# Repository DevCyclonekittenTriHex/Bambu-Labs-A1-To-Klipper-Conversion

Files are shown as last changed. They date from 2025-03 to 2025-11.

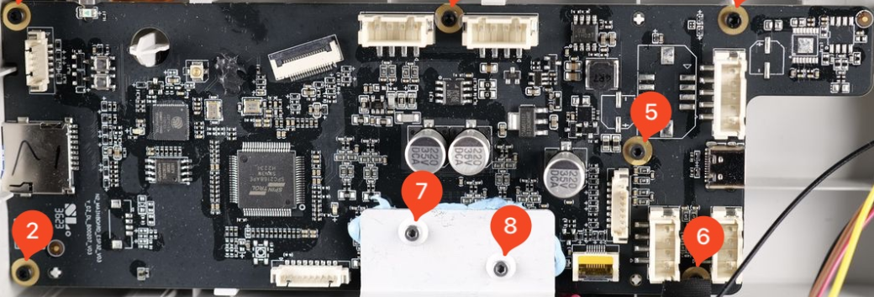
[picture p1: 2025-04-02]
OLDSTUFF/KicadImages/a1mb.png

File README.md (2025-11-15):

## Bambu Lab A1 Klipper Conversion (In development)

## Join Chaz's [**Discord Server**](https://discord.gg/W6B5mBejuC) to help with all bambu labs klipper mods.

> [!Caution]
> Doing any modifications may void your warrenty! 
> [!Caution]
> This Project is in currently not finished, this conversion is done fully at your own risk, I am not liable for any damages done to your machine.

This is constantly being updated, the docs for the conversion will be [Here!](https://devcyclonekittentrihex.github.io/A1K-Documentation/Docs/)

# Aim
The aim of this open source project is to create drop in circuit boards for the Bambu Labs A1 and A1 mini machines; and to provide a good framework to promote modding of these machines. This project will try to intergrate every part from the original printer to make the upgrade seamless. This will give back people privacy and a fully lan or offline system to print.

Currently, I have designed the a1 mainboard and a1/a1m toolhead boards, and am currently going through revisioning.
My target for the pcbs are to order them by November 30th

# Functions

Does work:
- Full hotend heating 
- XYZ Movement
- Stock Part Cooling Fans
- Auto Bed Levelling (with biqu microprobe)
- Filament Runout (with biqu sfs2)

Does not work:
- Heated Bed : Currently have the pinout for it, will be implemented in pcbs.
- Filament Sensor : It is a linear hall sensor, pinout unknown. Will attempt to find.
- AMS Lite : Closed source, other open mmus are compatible
- Display : An unidentified display that is possibly using 4SPI

# Previous Experiments
I previously hooked up an skr pico to the printer, and got it printing without a heated bed. Here is the footage. I also killed my mainboard so there is no more footage.
https://youtu.be/fLf-GMceLxE

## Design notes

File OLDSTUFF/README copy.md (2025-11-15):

## Bambu Lab A1 Klipper Conversion (In development)

## Join Chaz's [**Discord Server**](https://discord.gg/W6B5mBejuC) to help.

> [!Caution]
> Doing any modifications may void your warrenty!
> This Project is in currently not finished, this conversion is done fully at your own risk, I am not liable for any damages done to your machine. 

The aim of this project is to add klipper functional to the powerful Bambu Labs A1.
Due to the recent push for "privacy and security", people are wanting to add freedom back to their machines.

This is constantly being updated, the docs for the conversion will be [Here!](https://devcyclonekittentrihex.github.io/A1K-Documentation/Docs/)

# Functions that don't work:
If you have any imformation about this, please contact me.
- Filament Sensor : Its a ribbon cable with a linear hall sensor (detects magnets and is analoge)
- Display : (Unidentified Ribbon cable, bbl says on a1m page that its 4spi)
- AMS lite : Closed Source (possibly openamsl, or get open source mmu) 
- Heated Bed : I am unable to get a solid state relay currently, but it is really easy to do.
- Solid state relay board, it is controlled by a ribbon cable by 8, idk pinout.
- 
# PCBing:
I am currently working on some pcbs, the mainboard and toolhead board are nearly done but are encoutering some issues in development.
I will purchase through jlcpcb, the toolhead board price for 2 boards is around 60 aud without shipping.

# Current Progress
This is my 2nd print (voron cube first), the part cooling fan wasn't working in it and there was a layer shift.
https://youtu.be/fLf-GMceLxE

# EDIT, SKR PICO KILLED (20/07/2025)
I am stupid and somehow killed my skr pico, this is probs gonna add a 2 week delay.

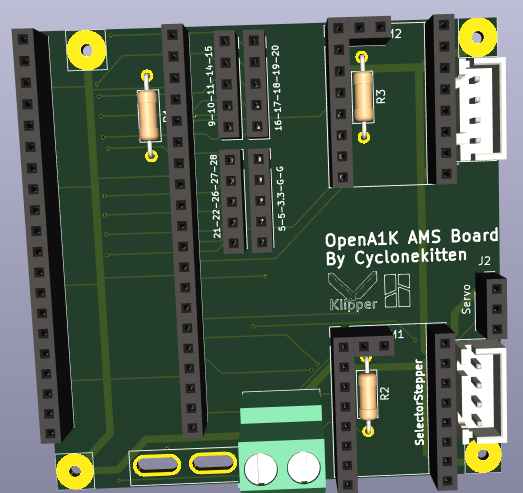
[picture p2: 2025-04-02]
OLDSTUFF/KicadImages/OpenA1K_AMSBoard.png

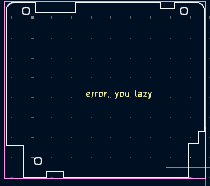
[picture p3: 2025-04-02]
OLDSTUFF/KicadImages/OpenA1K_THBoard.png

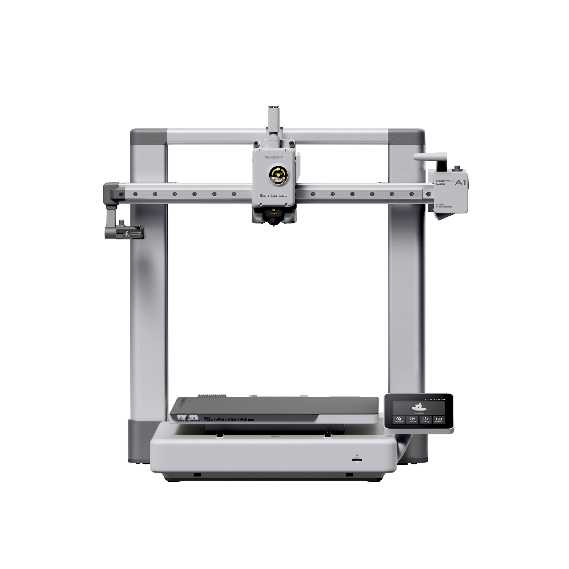
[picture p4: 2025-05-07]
OLDSTUFF/KicadImages/bbl_a1.png

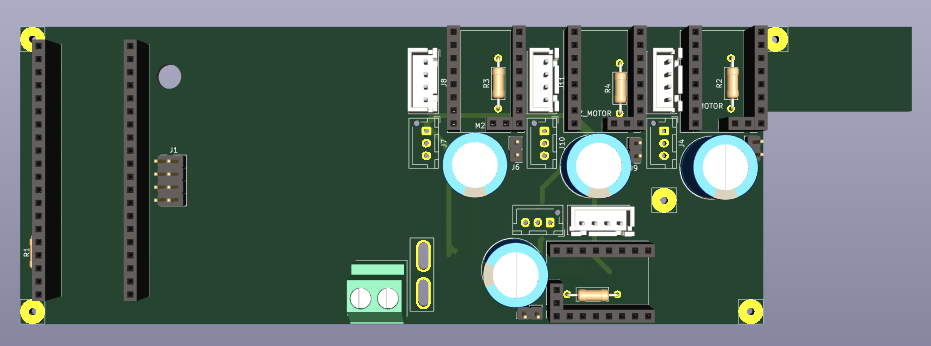
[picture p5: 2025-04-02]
OLDSTUFF/KicadImages/OpenA1K_MCUBoard.png

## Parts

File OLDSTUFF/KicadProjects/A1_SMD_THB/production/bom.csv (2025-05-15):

Designator | Footprint | Quantity | Value | LCSC Part #
C1, C4 | 0603 | 2 | 1uF | C15849
C10, C11, C14, C22, C28, C29, C3, C30, C5, C6, C7, C8, C9 | 0402 | 13 | 100nF
C12 | 0805 | 1 | 10uF | C15850
C13, C17, C18 | 0805 | 3 | 10uF
C15, C16 | 0402 | 2 | 15pF | C1548
C2 | 0402 | 1 | 100nF | C1525
C20, C25 | CP_Elec_8x10 | 2 | 100uF | C970687
C21 | 0603 | 1 | 22nF 50V | C21122
C23 | 0603 | 1 | 4.7uF | C19666
C24, C26 | 0603 | 2 | 100nF 50V
C27 | 0603 | 1 | 100nF 50V | C14663
D5 | SOT-23 | 1 | BAV99 | C2500
EXM2 | JST_XH_B4B-XH-A_1x04_P2.50mm_Vertical | 1 | Conn_01x04
J1 | PinHeader_1x02_P2.54mm_Vertical | 1 | Conn_01x02_Pin
J16 | PinHeader_1x01_P2.54mm_Vertical | 1 | SFS1
J2 | PinHeader_1x04_P2.54mm_Vertical | 1 | Conn_01x04_Pin
J3 | JST_XH_B4B-XH-A_1x04_P2.50mm_Vertical | 1 | PCF
J4 | PinHeader_1x03_P2.54mm_Vertical | 1 | Conn_01x03_Pin
J5 | JST_XH_B5B-XH-A_1x05_P2.50mm_Vertical | 1 | EXF
J6 | JST_XH_B2B-XH-A_1x02_P2.50mm_Vertical | 1 | THO
J7 | JST_XH_B2B-XH-A_1x02_P2.50mm_Vertical | 1 | HE
J8 | JST_XH_B2B-XH-A_1x02_P2.50mm_Vertical | 1 | BL_PROBE
J9 | JST_XH_B3B-XH-A_1x03_P2.50mm_Vertical | 1 | BL_SERVO
P1 | USB_C_Receptacle_HCTL_HC-TYPE-C-16P-01A | 1 | USB_C_Plug | C165948
R1, R2 | 0402 | 2 | 27.4o | C26971
R10, R11, R12 | 0402 | 3 | 20kΩ | C25765
R3 | 0603 | 1 | 1ko | C21190
R5, R6 | 0603 | 2 | 1k | C21190
R8, R9 | 1206 | 2 | 100mΩ | C25334
U1 | QFN-56-1EP_7x7mm_P0.4mm_EP3.2x3.2mm | 1 | RP2040 | C2040
U2 | SOT-223-3_TabPin2 | 1 | NCP1117-1.5_SOT223
U3 | QFN50P500X500X90-29N | 1 | TMC2209-LA | C2150710
U4 | SOIC-8_5.3x5.3mm_P1.27mm | 1 | W25Q128JVS | C97521
Y1 | Crystal_SMD_Abracon_ABM8AIG-4Pin_3.2x2.5mm | 1 | ABM8-272-T3 | C20625731

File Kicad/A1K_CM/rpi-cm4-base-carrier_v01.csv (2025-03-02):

Reference | Quantity | Value | Footprint | Datasheet | Digi-Key_PN | MPN | Manufacturer | Part Description | AVAILABILITY | DESCRIPTION | MF | MP | PACKAGE | PRICE | STANDARD | Digi-Key_PN (Alt) | Field4 | Field5
CR1 | 1 | SMBJ5.0A-TR | footprints:SMBJ5.0A-TR |  | 497-3144-1-ND | SMBJ5.0A-TR | STMicroelectronics
D1 | 1 | LED Green | LED_SMD:LED_0603_1608Metric | ~ | 160-1478-1-ND | LTST-S270KGKT | Lite-On Inc. | Green 572nm LED Indication - Discrete 2.2V 2-SMD, No Lead
D2 | 1 | LED Red | LED_SMD:LED_0603_1608Metric | ~ | 160-1479-1-ND | LTST-S270KRKT | Lite-On Inc. | Red 620nm LED Indication - Discrete 2.2V 2-SMD, No Lead
J1 | 1 | DNP | Connector_PinHeader_2.54mm:PinHeader_1x10_P2.54mm_Vertical | ~
J2 | 1 | USB4105-GF-A | USB4105-GF-A:GCT_USB4105-GF-A |  | 2073-USB4105-GF-ACT-ND | USB4105-GF-A | GCT |  | Unavailable | USB - C _Type - C_ USB 2.0 Receptacle Connector 24 Position Surface Mount, Right Angle; Through Hole | Global Connector Technology | USB4105 | Package Analog Devices | None
J3 | 1 | SM04B-SRSS-TB(LF)(SN) | SM04B-SRSS-TB_LF__SN_:JST_SM04B-SRSS-TB(LF)(SN) |  | 455-1804-1-ND | SM04B-SRSS-TB(LF)(SN) | JST Sales America Inc. |  |  |  |  |  |  |  | Manufacturer recommendations
J4 | 1 | USB_OTG | CM4IO:USB_Micro-B_EDAC_UCON00686 | ~ | 609-4050-1-ND | 10103594-0001LF | Amphenol ICC (FCI)
JP1 | 1 | SolderJumper_2_Open | Jumper:SolderJumper-2_P1.3mm_Open_RoundedPad1.0x1.5mm | ~
Module1 | 1 | ComputeModule4-CM4 | CM4IO:Raspberry-Pi-4-Compute-Module |  | 2x H11615CT-ND | 2x DF40C-100DS-0.4V | Hirose |  |  |  |  |  |  |  |  | 2x H124602CT-ND | Hirose | 2x DF40C-100DS-0.4V
R1 R4 | 2 | 5.1k | Resistor_SMD:R_0603_1608Metric_Pad0.98x0.95mm_HandSolder | ~ | 311-5.10KHRCT-ND | RC0603FR-075K1L | Yageo
R2 R6 | 2 | 1k | Resistor_SMD:R_0603_1608Metric_Pad0.98x0.95mm_HandSolder | ~ | 311-1.00KHRCT-ND | RC0603FR-071KL | Yageo
R3 R5 | 2 | DNP | Resistor_SMD:R_0603_1608Metric_Pad0.98x0.95mm_HandSolder | ~
R7 R8 | 2 | 2.2K 1% | Resistor_SMD:R_0603_1608Metric_Pad0.98x0.95mm_HandSolder | ~ | 311-2.20KHRCT-ND | RC0603FR-072K2L | Yageo
U1 | 1 | 74LVC1G07SE-7 | Package_TO_SOT_SMD:SOT-353_SC-70-5 | http://www.ti.com/lit/sg/scyt129e/scyt129e.pdf | 74LVC1G07SE-7DICT-ND | 74LVC1G07SE-7 | Diodes Incorporated | Buffer, Non-Inverting 1 Element 1 Bit per Element Open Drain Output SOT-353
U2 | 1 | TPD2EUSB30 | Package_TO_SOT_SMD:Texas_DRT-3 | http://www.ti.com/lit/ds/symlink/tpd2eusb30a.pdf | 296-25509-1-ND | TPD2EUSB30DRTR | Texas Instruments

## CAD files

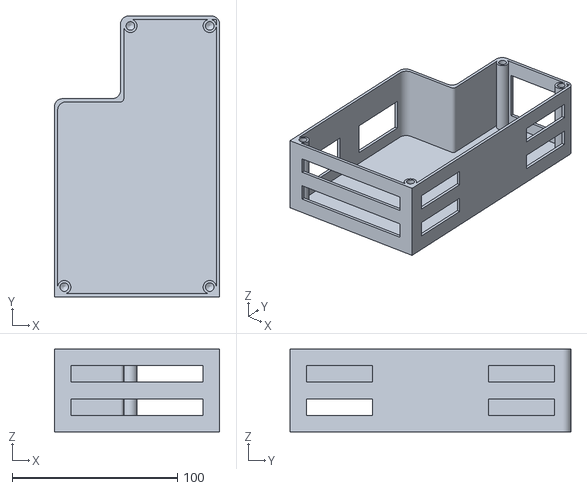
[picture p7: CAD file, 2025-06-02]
OLDSTUFF/PrintedFiles/Upgrades/mainboard_box-Body001.stl
100.0 x 170.0 x 50.0

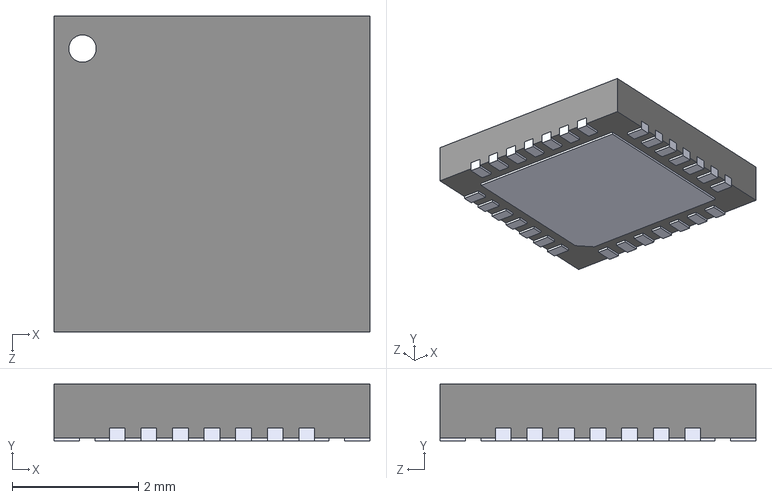
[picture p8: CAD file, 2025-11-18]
A1-Main-Board/footprints/TMC2209-LA.step
5.00 x 0.9 x 5.00 mm

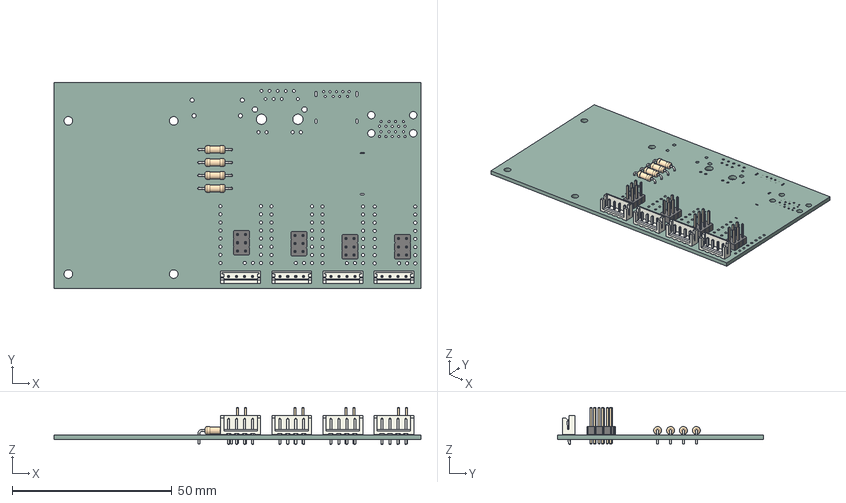
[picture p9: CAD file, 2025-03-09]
Kicad/A1K_CM/rpi-cm4-base-carrier.step
115.0 x 64.5 x 11.7 mm
JST_EH_B4B-EH-A_1x04_P2.50mm_Vertical x 4
PinHeader_2x03_P2.54mm_Vertical x 4
R_Axial_DIN0207_L6.3mm_D2.5mm_P10.16mm_Horizontal x 4
rpi-cm4-base-carrier_PCB

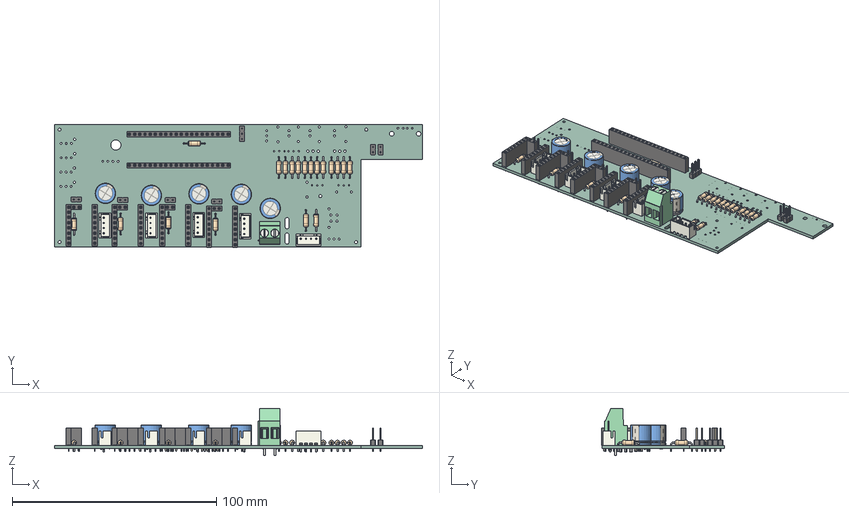
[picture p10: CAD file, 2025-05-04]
OLDSTUFF/KicadProjects/A1_MB.step
180.0 x 60.1 x 23.0 mm
JST_XH_B4B-XH-A_1x04_P2.50mm_Vertical x 5
R_Axial_DIN0207_L6.3mm_D2.5mm_P10.16mm_Horizontal x 19
PinHeader_1x02_P2.54mm_Vertical x 6
PinSocket_1x08_P2.54mm_Vertical x 8
PinSocket_1x02_P2.54mm_Vertical x 4
CP_Radial_D10.0mm_P5.00mm_P7.50mm x 5
PinHeader_1x03_P2.54mm_Vertical
PinSocket_1x20_P2.54mm_Vertical x 2
TerminalBlock_Phoenix_MKDS-3-2-5.08_1x02_P5.08mm_Horizontal
A1_MB_PCB

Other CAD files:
OLDSTUFF/PrintedFiles/Upgrades/mainboard_box.FCStd

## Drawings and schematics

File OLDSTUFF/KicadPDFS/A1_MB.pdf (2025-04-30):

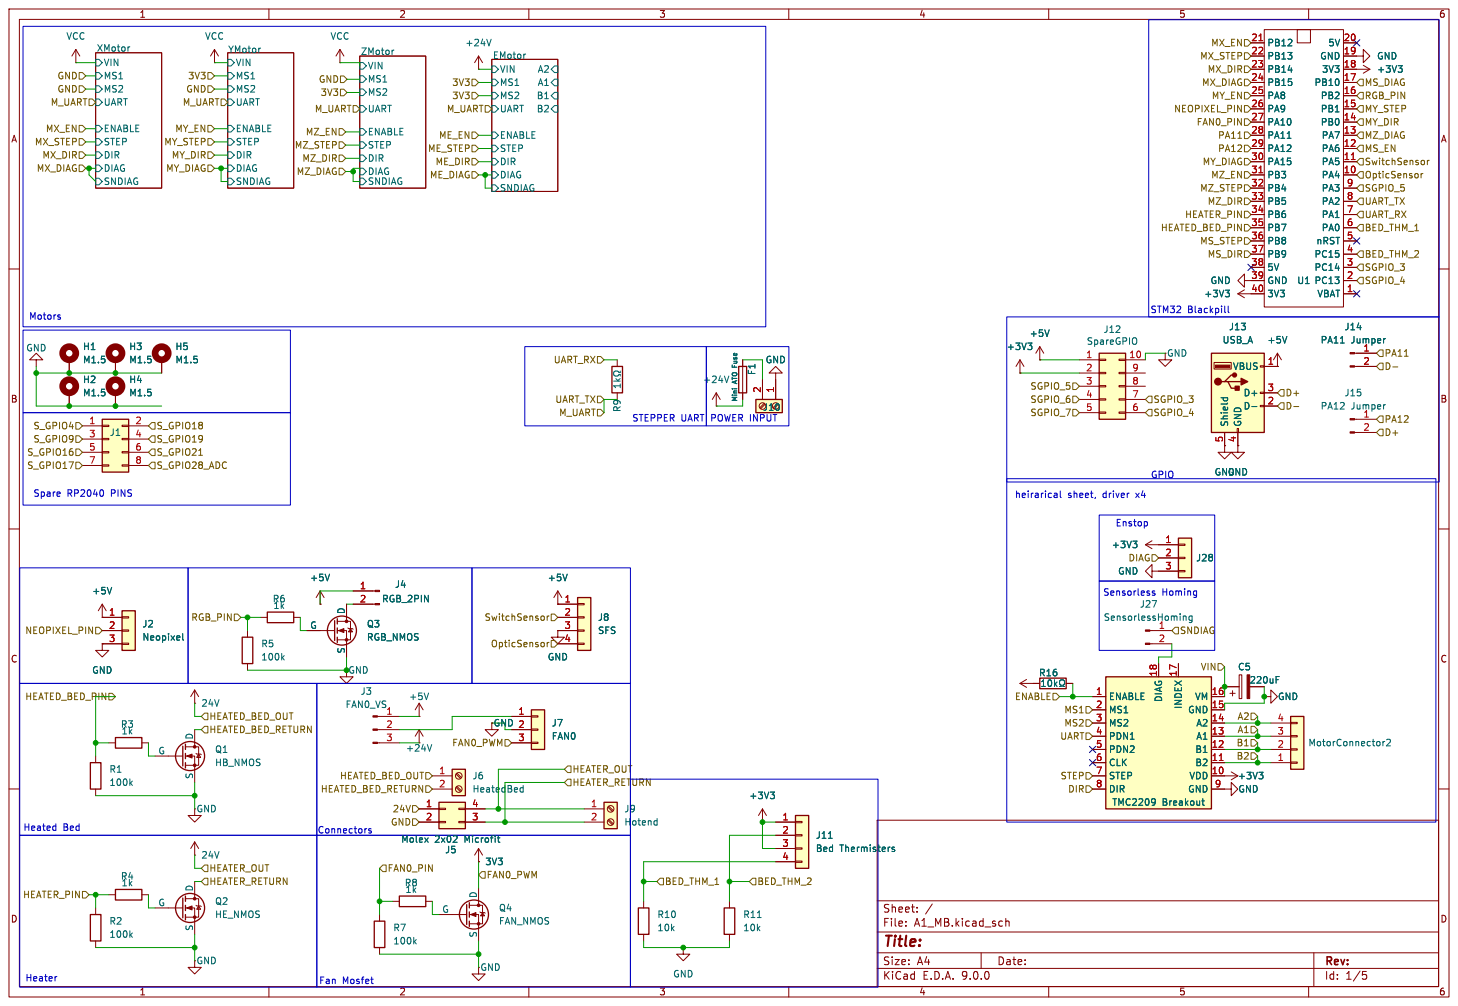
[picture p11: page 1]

Id: 1/5 Title: File: A1_MB.kicad_sch Sheet: /

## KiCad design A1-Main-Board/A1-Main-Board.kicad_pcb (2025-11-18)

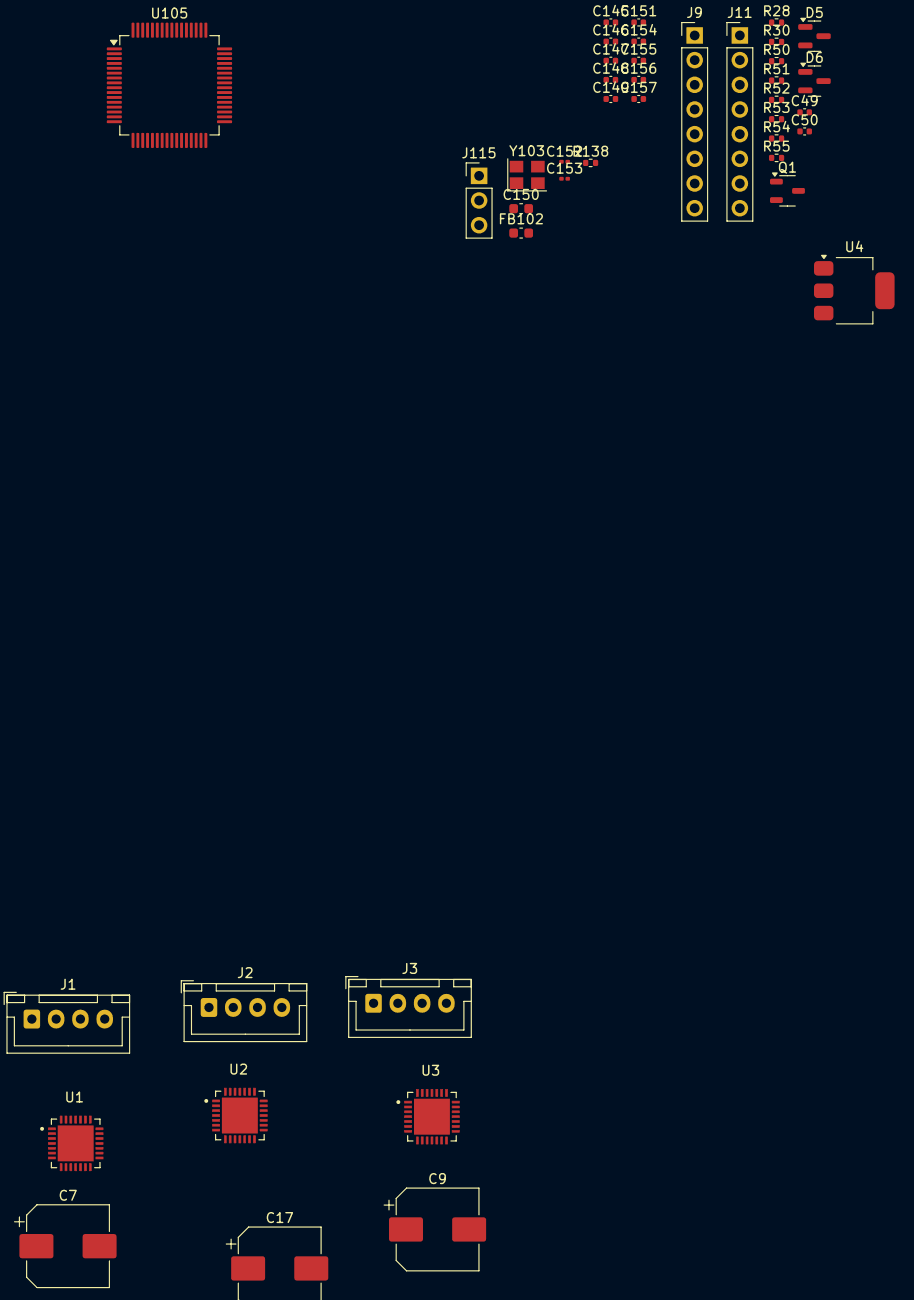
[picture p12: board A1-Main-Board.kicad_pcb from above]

Board: 2 copper layers, 43 parts (0 on the bottom side), 33 nets, no tracks yet.

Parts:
C7, C9, C17: 100uF; CP_Elec_8x10
C49, C50, C147, C148, C149, C154, C155, C156, C157: 100nF; C_0402_1005Metric
C145, C146: 30pF; C_0402_1005Metric
C150: 10uF; C_0603_1608Metric
C151: 10nF; C_0402_1005Metric
C152, C153: 1uF; C_0201_0603Metric
D5, D6: BAV99; SOT-23
FB102: 120r 100MHz; C_0603_1608Metric
J1, J2, J3: MotorJST; JST_XH_B4B-XH-A_1x04_P2.50mm_Vertical
J9: FPC1; PinHeader_1x08_P2.54mm_Vertical
J11: FPC2; PinHeader_1x08_P2.54mm_Vertical
J115: BOOT; PinHeader_1x03_P2.54mm_Vertical
Q1: NMOS; SOT-23-3
R28: 10R; R_0402_1005Metric
R30: 20kR; R_0402_1005Metric
R50, R53: 4.7kR; R_0402_1005Metric
R51, R52, R54, R55: 2.37kR; R_0402_1005Metric
R138: 10kR; R_0402_1005Metric
U1, U2, U3: TMC2209-LA
U4: AMS1117-3.3; SOT-223-3_TabPin2
U105: STM32G431RBT3; LQFP-64_10x10mm_P0.5mm
Y103: Crystal_GND24; Crystal_SMD_3225-4Pin_3.2x2.5mm

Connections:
+3V3: C147.1, C149.1, C150.1, C153.1, C154.1, C155.1, C156.1, C157.1, FB102.2, J115.1, U1.15 (VCC_IO), U2.9 (MS1_AD0), U2.15 (VCC_IO), U3.10 (MS2_AD1), U3.15 (VCC_IO), U105.1 (VBAT), U105.16 (VDD), U105.32 (VDD), U105.48 (VDD), U105.64 (VDD)
+3V3A: C151.1, C152.1, D5.2 (A), D6.2 (A), FB102.1, R50.1, R53.1, U105.28 (VREF+), U105.29 (VDDA)
+5V: J11.1, U1.8 (5VOUT), U2.8 (5VOUT), U3.8 (5VOUT)
+24V: C7.1, C9.1, C17.1, U1.22 (VS), U1.28 (VS), U2.22 (VS), U2.28 (VS), U3.22 (VS), U3.28 (VS)
/drivers/MA_UART: U1.14 (~PD_UART), U2.14 (~PD_UART), U3.14 (~PD_UART), U105.22 (PC4)
/heated-bed/10k_THB_INP: J11.4, R53.2, R54.1
/heated-bed/100k_THB_INP: J11.2, R50.2, R51.1
/heated-bed/BED_THERM_1: C49.1, R52.2, U105.36 (PB14)
/heated-bed/BED_THERM_2: C50.1, R55.2, U105.43 (PA9)
/heated-bed/HEATED_BED-: J11.7, Q1.1 (D)
/heated-bed/HEATED_BED_PWM: R28.1, R30.1, U105.38 (PC6)
GND: C7.2, C9.2, C17.2, C49.2, C50.2, C145.2, C146.2, C148.2, C151.2, C152.2, C153.2, D5.1 (K), D6.1 (K), J11.3, J11.5, J11.8, J115.3, Q1.3 (S), R30.2, U1.3 (GND), U1.9 (MS1_AD0), U1.10 (MS2_AD1), U1.18 (GND), U1.29 (EXP), U2.3 (GND), U2.10 (MS2_AD1), U2.18 (GND), U2.29 (EXP), U3.3 (GND), U3.9 (MS1_AD0), U3.18 (GND), U3.29 (EXP), U105.15 (VSS), U105.27 (VSSA), U105.31 (VSS), U105.47 (VSS), U105.63 (VSS), Y103.2, Y103.4
unnamed: C147.2, C149.2, C150.2, C154.2, C155.2, C156.2, C157.2
unnamed: D5.3 (K), R51.2, R52.1
unnamed: D6.3 (K), R54.2, R55.1
unnamed: J1.1, U1.24 (OA1)
unnamed: J1.2, U1.26 (OB1)
unnamed: J1.3, U1.21 (OA2)
unnamed: J1.4, U1.1 (OB2)
unnamed: J2.1, U2.24 (OA1)
unnamed: J2.2, U2.26 (OB1)
unnamed: J2.3, U2.21 (OA2)
unnamed: J2.4, U2.1 (OB2)
unnamed: J3.1, U3.24 (OA1)
unnamed: J3.2, U3.26 (OB1)
unnamed: J3.3, U3.21 (OA2)
unnamed: J3.4, U3.1 (OB2)
unnamed: J115.2, R138.1
unnamed: Q1.2 (G), R28.2
unnamed: C148.1, U105.7 (PG10)
unnamed: R138.2, U105.61 (PB8)
unnamed: C145.1, U105.5 (PF0), Y103.1
unnamed: C146.1, U105.6 (PF1), Y103.3

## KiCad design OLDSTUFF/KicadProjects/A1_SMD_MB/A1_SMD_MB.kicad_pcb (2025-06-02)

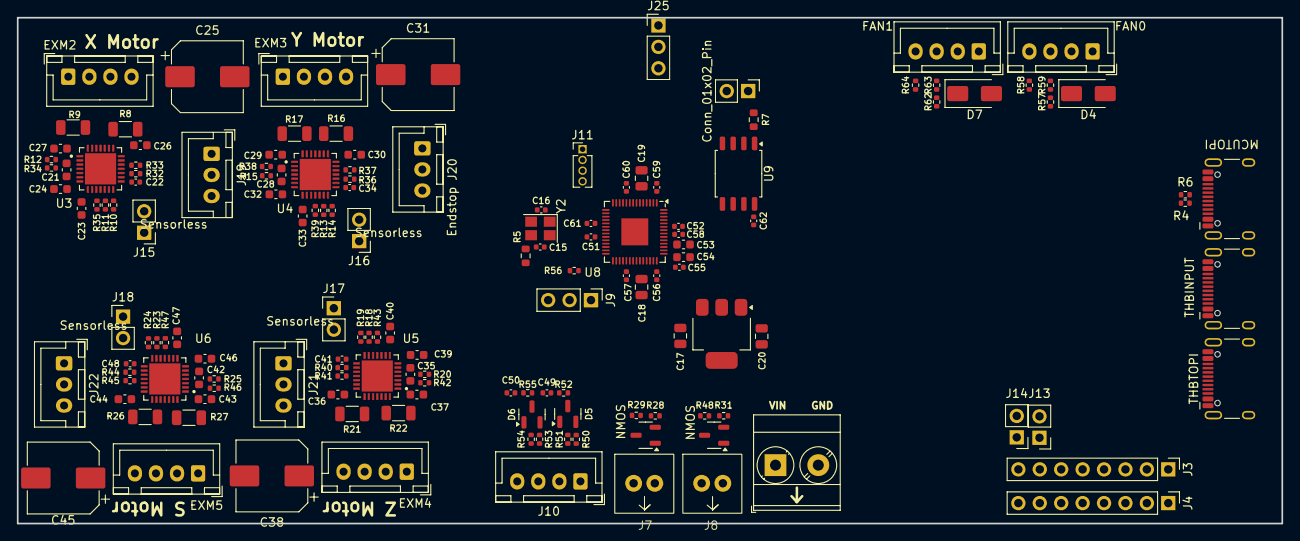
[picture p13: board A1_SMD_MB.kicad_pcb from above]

Board: 2 copper layers, 150.0 x 60.0 mm, 148 parts (0 on the bottom side), 134 nets, no tracks yet.

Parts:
C15, C16: 15pF; C_0402_1005Metric
C17, C18, C19, C20: 10uF; C_0805_2012Metric
C21, C28, C35, C42: 22nF 50V; C_0603_1608Metric
C22, C34, C41, C48, C49, C50, C51, C52, C55, C56, C57, C58, C59, C60, C61, C62: 100nF; C_0402_1005Metric
C23, C33, C40, C47: 4.7uF; C_0603_1608Metric
C24, C26, C27, C29, C30, C32, C36, C37, C39, C43, C44, C46: 100nF 50V; C_0603_1608Metric
C25, C31, C38, C45: 100uF; CP_Elec_8x10
C53, C54: 1uF; C_0603_1608Metric
D4, D7: D; D_SMA
D5, D6: BAV99; SOT-23
EXM2, EXM3, EXM4, EXM5: Conn_01x04; JST_XH_B4B-XH-A_1x04_P2.50mm_Vertical
J3: FPC2; PinHeader_1x08_P2.54mm_Vertical
J4: FPC1; PinHeader_1x08_P2.54mm_Vertical
J6: FAN0; JST_XH_B4B-XH-A_1x04_P2.50mm_Vertical
J7: HE; ScrewTerminal 7mm x 7mm
J8: HB; ScrewTerminal 7mm x 7mm
J9: Conn_01x03_Pin; PinHeader_1x03_P2.54mm_Vertical
J10: BedTherms; JST_XH_B4B-XH-A_1x04_P2.50mm_Vertical
J11: SWD; PinHeader_1x04_P1.27mm_Vertical
J12: Conn_01x02_Pin; PinHeader_1x02_P2.54mm_Vertical
J13: THM2JMP; PinHeader_1x02_P2.54mm_Vertical
J14: THM1JMP; PinHeader_1x02_P2.54mm_Vertical
J15, J16, J17, J18: Sensorless; PinHeader_1x02_P2.54mm_Vertical
J19, J20, J21, J22: Endstop; JST_XH_B3B-XH-A_1x03_P2.50mm_Vertical
J23: PWR; 1x2 Terminal Block
J24: FAN1; JST_XH_B4B-XH-A_1x04_P2.50mm_Vertical
J25: SPR_IO; PinHeader_1x03_P2.54mm_Vertical
P1: MCUTOPI; USB_C_Receptacle_HCTL_HC-TYPE-C-16P-01A
P2: THBINPUT; USB_C_Receptacle_HCTL_HC-TYPE-C-16P-01A
P3: THBTOPI; USB_C_Receptacle_HCTL_HC-TYPE-C-16P-01A
Q1, Q2: NMOS; SOT-23-3
R4, R6: 27.4o; R_0402_1005Metric
R5: 1k; R_0603_1608Metric
R7: 1ko; R_0603_1608Metric
R8, R9, R16, R17, R21, R22, R26, R27: 100mΩ; R_1206_3216Metric
R10, R11, R12, R13, R14, R15, R18, R19, R20, R23, R24, R25: 20kΩ; R_0402_1005Metric
R28, R31: 10R; R_0402_1005Metric
R29, R48, R58, R64: 20kR; R_0402_1005Metric
R32, R33, R34, R35, R36, R37, R38, R39, R40, R41, R42, R43, R44, R45, R46, R47: 100o; R_0402_1005Metric
R50, R53: 4.7kR; R_0402_1005Metric
R51, R52, R54, R55: 2.37kR; R_0402_1005Metric
R56: 10k; R_0402_1005Metric
R57, R59, R62, R63: 100R; R_0402_1005Metric
U3, U4, U5, U6: TMC2209-LA
U7: NCP1117-1.5_SOT223; SOT-223-3_TabPin2
U8: RP2040; QFN-56-1EP_7x7mm_P0.4mm_EP3.2x3.2mm
U9: W25Q128JVS; SOIC-8_5.3x5.3mm_P1.27mm
Y2: ABM8-272-T3; Crystal_SMD_Abracon_ABM8AIG-4Pin_3.2x2.5mm

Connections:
+1V1: C51.1, C52.1, C53.1, U8.23 (DVDD), U8.45 (VREG_VOUT), U8.50 (DVDD)
+3.3VADC: D5.2 (A), D6.2 (A), R50.1, R53.1
+3V3: C18.1, C19.1, C20.1, C22.2, C34.2, C41.2, C48.2, C54.1, C55.1, C56.1, C57.1, C58.1, C59.1, C60.1, C61.1, C62.1, J3.5, J9.1, J11.1, R12.1, R15.1, R20.1, R25.1, U3.15 (VCC_IO), U4.9 (MS1_AD0), U4.15 (VCC_IO), U5.10 (MS2_AD1), U5.15 (VCC_IO), U6.9 (MS1_AD0), U6.10 (MS2_AD1), U6.15 (VCC_IO), U7.2 (VO), U8.1 (IOVDD), U8.10 (IOVDD), U8.22 (IOVDD), U8.33 (IOVDD), U8.42 (IOVDD), U8.43 (ADC_AVDD), U8.44 (VREG_IN), U8.48 (USB_VDD), U8.49 (IOVDD), U9.8 (VCC)
+5V: C23.2, C33.2, C40.2, C47.2, J3.1, J3.2, J19.3, J20.3, J21.3, J22.3, P2.A8 (SBU1), P2.B8 (SBU2), U3.8 (5VOUT), U4.8 (5VOUT), U5.8 (5VOUT), U6.8 (5VOUT)
+24V: C24.1, C25.1, C26.2, C27.2, C29.2, C30.2, C31.1, C32.1, C36.2, C37.2, C38.1, C39.1, C43.2, C44.2, C45.1, C46.1, D4.2 (A), D7.2 (A), J6.1, J7.1, J8.1, J23.1, J24.1, P2.A4 (VBUS), P2.A9 (VBUS), P2.B4 (VBUS), P2.B9 (VBUS), U3.22 (VS), U3.28 (VS), U4.22 (VS), U4.28 (VS), U5.22 (VS), U5.28 (VS), U6.22 (VS), U6.28 (VS)
/Motors/MS_DIAG: J22.1, R47.2, U8.34 (GPIO22)
/Motors/MS_DIR: R45.1, U8.32 (GPIO21)
/Motors/MS_EN: R46.1, U8.30 (GPIO19)
/Motors/MS_STEP: R44.1, U8.31 (GPIO20)
/Motors/MX_DIAG: J19.1, R35.2, U8.13 (GPIO10)
/Motors/MX_DIR: R33.1, U8.12 (GPIO9)
/Motors/MX_EN: R34.1, U8.9 (GPIO7)
/Motors/MX_STEP: R32.1, U8.11 (GPIO8)
/Motors/MY_DIAG: J20.1, R39.2, U8.17 (GPIO14)
/Motors/MY_DIR: R37.1, U8.16 (GPIO13)
/Motors/MY_EN: R38.1, U8.14 (GPIO11)
/Motors/MY_STEP: R36.1, U8.15 (GPIO12)
/Motors/MZ_DIAG: J21.1, R43.2, U8.29 (GPIO18)
/Motors/MZ_DIR: R41.1, U8.28 (GPIO17)
/Motors/MZ_EN: R42.1, U8.18 (GPIO15)
/Motors/MZ_STEP: R40.1, U8.27 (GPIO16)
/Motors/UART: R10.2, R14.2, R19.2, R24.2, U3.14 (~PD_UART), U4.14 (~PD_UART), U5.14 (~PD_UART), U6.14 (~PD_UART), U8.8 (GPIO6)
/fpc/HB_CT: J3.6, U8.6 (GPIO4)
/fpc/THM1: C50.1, J14.2, R55.2, U8.41 (GPIO29_ADC3)
/fpc/THM2: C49.1, J13.2, R52.2, U8.40 (GPIO28_ADC2)
/mcu/G1: R58.1, U8.3 (GPIO1)
/mcu/G2: R31.1, R48.1, U8.4 (GPIO2)
/mcu/G3: R28.1, R29.1, U8.5 (GPIO3)
/mcu/G23: J25.1, U8.35 (GPIO23)
/mcu/G24: J25.2, U8.36 (GPIO24)
/mcu/G25: J25.3, U8.37 (GPIO25)
/mcu/G26: R62.1, U8.38 (GPIO26_ADC0)
/mcu/G27: R64.1, U8.39 (GPIO27_ADC1)
/mcu/GPIO0: R57.1, U8.2 (GPIO0)
/mcu/IO0: U8.53 (QSPI_SD0), U9.5 (DI/IO_{0})
/mcu/IO1: U8.55 (QSPI_SD1), U9.2 (DO/IO_{1})
/mcu/IO2: U8.54 (QSPI_SD2), U9.3 (~WP/IO_{2})
/mcu/IO3: U8.51 (QSPI_SD3), U9.7 (~HOLD/~RESET/IO_{3})
/mcu/IO_CLK: U8.52 (QSPI_SCLK), U9.6 (CLK)
/mcu/IO_CS: R7.2, U8.56 (QSPI_SS), U9.1 (~CS)
/mcu/USB_D+: P1.A6 (D+), R4.1
/mcu/USB_D-: P1.A7 (D-), R6.1
/mcu/XIN: C16.2, U8.20 (XIN), Y2.1
/mcu/XOUT: R5.2, U8.21 (XOUT)
/stuff/HB_S: Q2.2 (G), R31.2
/stuff/HE_S: Q1.2 (G), R28.2
GND: C22.1, C23.1, C25.2, C26.1, C27.1, C29.1, C30.1, C31.2, C33.1, C34.1, C36.1, C37.1, C38.2, C40.1, C41.1, C43.1, C44.1, C45.2, C47.1, C48.1, C49.2, C50.2, D4.1 (K), D5.1 (K), D6.1 (K), D7.1 (K), J3.3, J3.4, J6.2, J10.2, J10.4, J19.2, J20.2, J21.2, J22.2, J23.2, J24.2, P1.A1 (GND), P1.A12 (GND), P1.B1 (GND), P1.B12 (GND), P1.S1 (SHIELD), P2.A1 (GND), P2.A12 (GND), P2.B1 (GND), P2.B12 (GND), P2.S1 (SHIELD), P3.A1 (GND), P3.A12 (GND), P3.B1 (GND), P3.B12 (GND), P3.S1 (SHIELD), Q1.3 (S), Q2.3 (S), R8.2, R9.2, R10.1, R11.1, R13.1, R14.1, R16.2, R17.2, R18.1, R19.1, R21.2, R22.2, R23.1, R24.1, R26.2, R27.2, R29.2, R48.2, U3.3 (GND), U3.9 (MS1_AD0), U3.10 (MS2_AD1), U3.18 (GND), U3.29 (EXP), U4.3 (GND), U4.10 (MS2_AD1), U4.18 (GND), U4.29 (EXP), U5.3 (GND), U5.9 (MS1_AD0), U5.18 (GND), U5.29 (EXP), U6.3 (GND), U6.18 (GND), U6.29 (EXP)
GND3: C15.1, C16.1, C17.2, C18.2, C19.2, C20.2, C51.2, C52.2, C53.2, C54.2, C55.2, C56.2, C57.2, C58.2, C59.2, C60.2, C61.2, C62.2, J9.3, J11.4, J12.2, U7.1 (GND), U8.19 (TESTEN), U8.57 (GND), U9.4 (GND), Y2.2, Y2.4
unnamed: C15.2, R5.1, Y2.3
unnamed: D5.3 (K), R51.2, R52.1
unnamed: D6.3 (K), R54.2, R55.1
unnamed: EXM2.1, U3.1 (OB2)
unnamed: EXM2.2, U3.26 (OB1)
unnamed: EXM2.3, U3.24 (OA1)
unnamed: EXM2.4, U3.21 (OA2)
unnamed: EXM3.1, U4.1 (OB2)
unnamed: EXM3.2, U4.26 (OB1)
unnamed: EXM3.3, U4.24 (OA1)
unnamed: EXM3.4, U4.21 (OA2)
unnamed: EXM4.1, U5.1 (OB2)
unnamed: EXM4.2, U5.26 (OB1)
unnamed: EXM4.3, U5.24 (OA1)
unnamed: EXM4.4, U5.21 (OA2)
unnamed: EXM5.1, U6.1 (OB2)
unnamed: EXM5.2, U6.26 (OB1)
unnamed: EXM5.3, U6.24 (OA1)
unnamed: EXM5.4, U6.21 (OA2)
unnamed: J6.3, R59.2
unnamed: J6.4, R58.2
unnamed: J7.2, Q1.1 (D)
unnamed: J8.2, Q2.1 (D)
unnamed: J9.2, R56.1
unnamed: J10.1, R50.2, R51.1
unnamed: J10.3, R53.2, R54.1
unnamed: J11.2, U8.24 (SWCLK)
unnamed: J11.3, U8.25 (SWD)
unnamed: J12.1, R7.1
unnamed: J3.7, J13.1
unnamed: J3.8, J14.1
unnamed: J15.1, R35.1
unnamed: J15.2, U3.11 (DIAG)
unnamed: J16.1, R39.1
unnamed: J16.2, U4.11 (DIAG)
unnamed: J17.1, R43.1
unnamed: J17.2, U5.11 (DIAG)
unnamed: J18.1, R47.1
unnamed: J18.2, U6.11 (DIAG)
unnamed: J24.3, R63.2
unnamed: J24.4, R64.2
unnamed: P2.A5 (CC), P2.B5 (VCONN)
unnamed: P2.A6 (D+), P3.A6 (D+)
unnamed: P2.A7 (D-), P3.A7 (D-)
unnamed: R57.2, R59.1
unnamed: R62.2, R63.1
unnamed: R8.1, U3.23 (BRA)
unnamed: R9.1, U3.27 (BRB)
unnamed: R11.2, U3.13 (CLK)
unnamed: C21.1, U3.5 (CPI)
unnamed: C21.2, U3.4 (CPO)
unnamed: R33.2, U3.19 (DIR)
unnamed: R32.2, U3.16 (STEP)
unnamed: C24.2, U3.6 (VCP)
unnamed: R12.2, R34.2, U3.2 (~EN)
unnamed: R16.1, U4.23 (BRA)
unnamed: R17.1, U4.27 (BRB)
unnamed: R13.2, U4.13 (CLK)
unnamed: C28.1, U4.5 (CPI)
unnamed: C28.2, U4.4 (CPO)
unnamed: R37.2, U4.19 (DIR)
unnamed: R36.2, U4.16 (STEP)
unnamed: C32.2, U4.6 (VCP)
unnamed: R15.2, R38.2, U4.2 (~EN)
unnamed: R21.1, U5.23 (BRA)
unnamed: R22.1, U5.27 (BRB)
unnamed: R18.2, U5.13 (CLK)
unnamed: C35.1, U5.5 (CPI)
unnamed: C35.2, U5.4 (CPO)
unnamed: R41.2, U5.19 (DIR)
unnamed: R40.2, U5.16 (STEP)
unnamed: C39.2, U5.6 (VCP)
unnamed: R20.2, R42.2, U5.2 (~EN)
unnamed: R26.1, U6.23 (BRA)
unnamed: R27.1, U6.27 (BRB)
unnamed: R23.2, U6.13 (CLK)
unnamed: C42.1, U6.5 (CPI)
unnamed: C42.2, U6.4 (CPO)
unnamed: R45.2, U6.19 (DIR)
unnamed: R44.2, U6.16 (STEP)
unnamed: C46.2, U6.6 (VCP)
unnamed: R25.2, R46.2, U6.2 (~EN)
unnamed: R56.2, U8.26 (RUN)
unnamed: R6.2, U8.46 (USB_DM)
unnamed: R4.2, U8.47 (USB_DP)
VBUS: C17.1, P1.A4 (VBUS), P1.A9 (VBUS), P1.B4 (VBUS), P1.B9 (VBUS), P3.A4 (VBUS), P3.A9 (VBUS), P3.B4 (VBUS), P3.B9 (VBUS), U7.3 (VI)

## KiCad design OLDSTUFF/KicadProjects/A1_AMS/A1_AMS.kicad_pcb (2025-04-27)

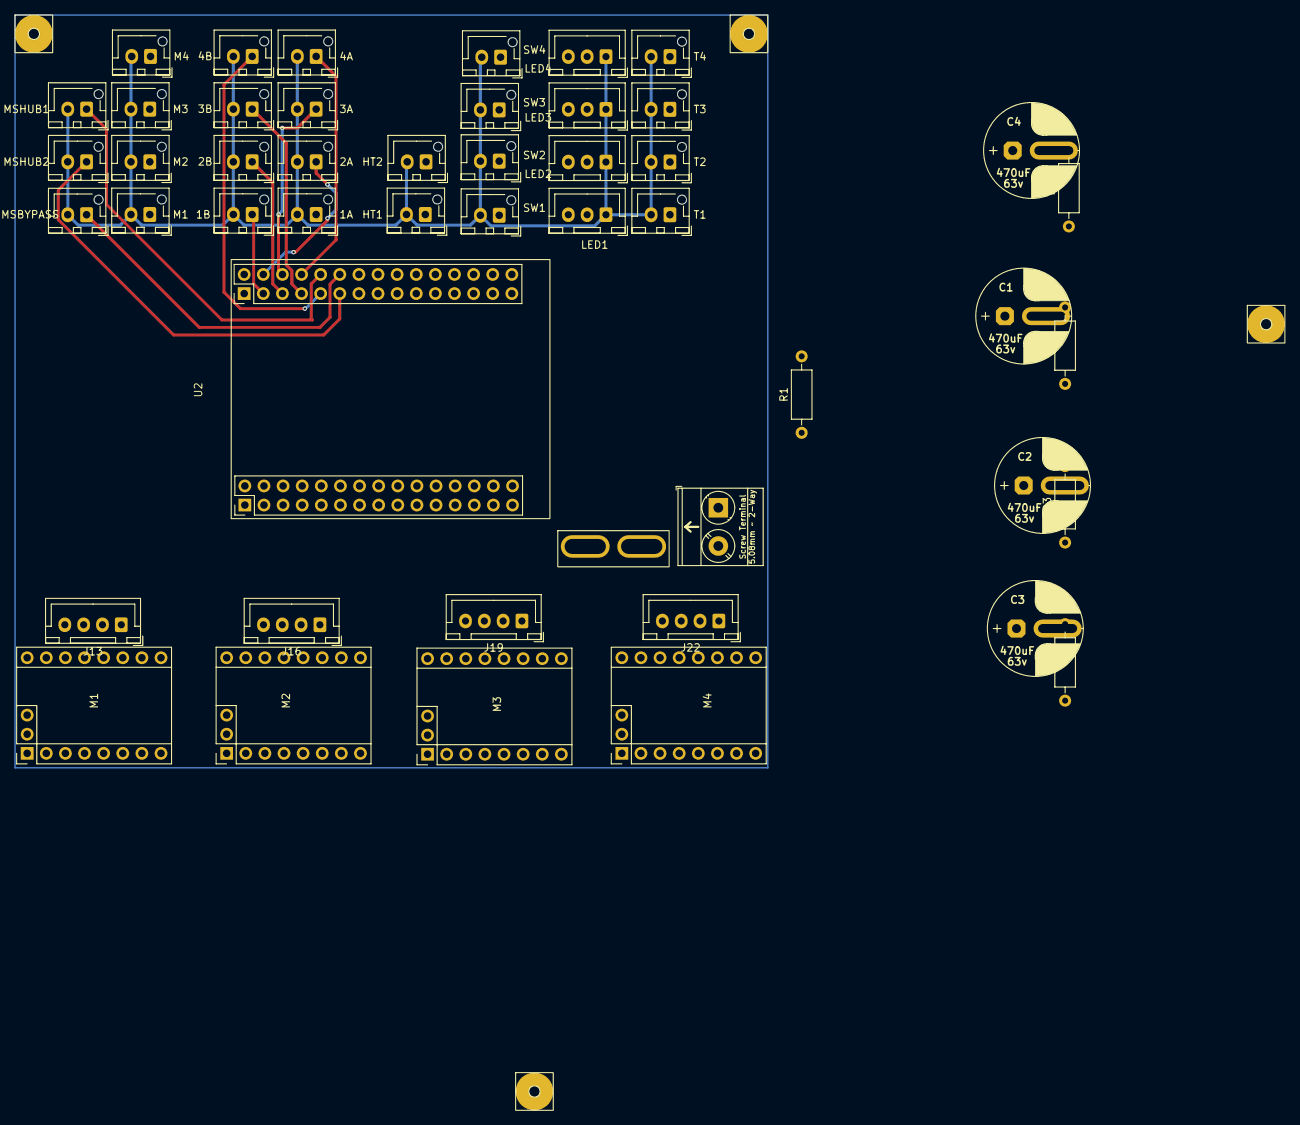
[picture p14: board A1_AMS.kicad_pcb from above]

Board: 2 copper layers, 53 parts (0 on the bottom side), 60 nets.

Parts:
C1, C2, C3, C4: 470uF; Cap ~ 12.5, 2.5mm-7.5mm pitch
F1: Mini ATO Fuse; Updated ATO Mini-Blade_2Post
H1, H2, H4, H5: M1.5; Mountinghole_m1.5
J1: 1A; JST_XH_B2B-XH-AM_1x02_P2.50mm_Vertical
J2: 2A; JST_XH_B2B-XH-AM_1x02_P2.50mm_Vertical
J3: 3A; JST_XH_B2B-XH-AM_1x02_P2.50mm_Vertical
J4: 4A; JST_XH_B2B-XH-AM_1x02_P2.50mm_Vertical
J5: LED1; JST_XH_B3B-XH-A_1x03_P2.50mm_Vertical
J6: 1B; JST_XH_B2B-XH-AM_1x02_P2.50mm_Vertical
J7: 2B; JST_XH_B2B-XH-AM_1x02_P2.50mm_Vertical
J8: 3B; JST_XH_B2B-XH-AM_1x02_P2.50mm_Vertical
J9: 4B; JST_XH_B2B-XH-AM_1x02_P2.50mm_Vertical
J10: Screw_Terminal_01x02; 1x2 Terminal Block
J11: M1; JST_XH_B2B-XH-AM_1x02_P2.50mm_Vertical
J12: M2; JST_XH_B2B-XH-AM_1x02_P2.50mm_Vertical
J13, J16, J19, J22: Conn_01x04; JST_XH_B4B-XH-A_1x04_P2.50mm_Vertical
J14: M4; JST_XH_B2B-XH-AM_1x02_P2.50mm_Vertical
J15: M3; JST_XH_B2B-XH-AM_1x02_P2.50mm_Vertical
J17: LED2; JST_XH_B3B-XH-A_1x03_P2.50mm_Vertical
J18: LED3; JST_XH_B3B-XH-A_1x03_P2.50mm_Vertical
J20: LED4; JST_XH_B3B-XH-A_1x03_P2.50mm_Vertical
J21: SW1; JST_XH_B2B-XH-AM_1x02_P2.50mm_Vertical
J23: SW2; JST_XH_B2B-XH-AM_1x02_P2.50mm_Vertical
J24: SW3; JST_XH_B2B-XH-AM_1x02_P2.50mm_Vertical
J25: MSHUB1; JST_XH_B2B-XH-AM_1x02_P2.50mm_Vertical
J26: MSHUB2; JST_XH_B2B-XH-AM_1x02_P2.50mm_Vertical
J27: MSBYPASS; JST_XH_B2B-XH-AM_1x02_P2.50mm_Vertical
J29: T1; JST_XH_B2B-XH-AM_1x02_P2.50mm_Vertical
J30: T2; JST_XH_B2B-XH-AM_1x02_P2.50mm_Vertical
J31: T3; JST_XH_B2B-XH-AM_1x02_P2.50mm_Vertical
JS4: SW4; JST_XH_B2B-XH-AM_1x02_P2.50mm_Vertical
JS5: T4; JST_XH_B2B-XH-AM_1x02_P2.50mm_Vertical
JS6: HT1; JST_XH_B2B-XH-AM_1x02_P2.50mm_Vertical
JS7: HT2; JST_XH_B2B-XH-AM_1x02_P2.50mm_Vertical
M1, M2, M3, M4: TMC2209 Breakout; TMC2209 Footprint
R1: 1kΩ; R_Axial_DIN0207_L6.3mm_D2.5mm_P10.16mm_Horizontal
R2, R3, R4, R5: 10kΩ; R_Axial_DIN0207_L6.3mm_D2.5mm_P10.16mm_Horizontal
U2: Socketed MCU STM32 64P

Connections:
+3V3: M1.10 (VDD), M2.10 (VDD), M3.10 (VDD), M4.10 (VDD), R2.2, R3.2, R4.2, R5.2
/3V3: M2.2 (MS1), M3.3 (MS2), M4.2 (MS1), M4.3 (MS2)
/5V: J5.3, J17.3, J18.3, J20.3
/AMotor/A1: J13.3, M1.13 (A1)
/AMotor/A2: J13.4, M1.14 (A2)
/AMotor/B1: J13.2, M1.12 (B1)
/AMotor/B2: J13.1, M1.11 (B2)
/BMotor/A1: J16.3, M2.13 (A1)
/BMotor/A2: J16.4, M2.14 (A2)
/BMotor/B1: J16.2, M2.12 (B1)
/BMotor/B2: J16.1, M2.11 (B2)
/CMotor/A1: J19.3, M3.13 (A1)
/CMotor/A2: J19.4, M3.14 (A2)
/CMotor/B1: J19.2, M3.12 (B1)
/CMotor/B2: J19.1, M3.11 (B2)
/DMotor/A1: J22.3, M4.13 (A1)
/DMotor/A2: J22.4, M4.14 (A2)
/DMotor/B1: J22.2, M4.12 (B1)
/DMotor/B2: J22.1, M4.11 (B2)
/HT_C1: JS6.1, U2.43 (PA12)
/HT_C2: JS7.1, U2.44 (PA15)
/LED_1: J5.2, U2.49 (PC8)
/LED_2: J17.2, U2.50 (PC9)
/LED_3: J18.2, U2.51 (PC6)
/LED_4: J20.2, U2.52 (PC7)
/MA_DIR: M1.8 (DIR), U2.5 (PC0)
/MA_EN: M1.1 (ENABLE), R2.1, U2.3 (PC14)
/MA_STEP: M1.7 (STEP), U2.4 (PC13)
/MB_DIR: M2.8 (DIR), U2.8 (PC1)
/MB_EN: M2.1 (ENABLE), R3.1, U2.6 (PC15)
/MB_STEP: M2.7 (STEP), U2.7 (PC2)
/MC_DIR: M3.8 (DIR), U2.11 (PA2)
/MC_EN: M3.1 (ENABLE), R4.1, U2.9 (PA0)
/MC_STEP: M3.7 (STEP), U2.10 (PC3)
/MD_DIR: M4.8 (DIR), U2.14 (PA3)
/MD_EN: M4.1 (ENABLE), R5.1, U2.12 (PA1)
/MD_STEP: M4.7 (STEP), U2.13 (PA4)
/MS_1A: J1.1, U2.31 (PB9)
/MS_1B: J6.1, U2.33 (PB7)
/MS_2A: J2.1, U2.34 (PB8)
/MS_2B: J7.1, U2.35 (PB5)
/MS_3A: J3.1, U2.36 (PB6)
/MS_3B: J8.1, U2.37 (PB3)
/MS_4A: J4.1, U2.38 (PB4)
/MS_4B: J9.1, U2.39 (PC12)
/MS_BYPASS: J27.1, U2.42 (PC11)
/MS_HUB1: J25.1, U2.40 (PD2)
/MS_HUB2: J26.1, U2.41 (PC10)
/M_UART: M1.4 (PDN1), M2.4 (PDN1), M4.4 (PDN1), R1.2
/M_VBUS: C1.1, C2.1, C3.1, C4.1, F1.1, M1.16 (VM), M2.16 (VM), M3.16 (VM), M4.16 (VM)
/SW_1: J21.1, U2.45 (PA10)
/SW_2: J23.1, U2.46 (PA11)
/SW_3: J24.1, U2.47 (PA8)
/SW_4: JS4.1, U2.48 (PA9)
/THM_1: J29.1, U2.53 (PB14)
/THM_2: J30.1, U2.54 (PB15)
/THM_3: J31.1, U2.55 (PB12)
/THM_4: JS5.1, U2.56 (PB13)
/VIN: F1.2, J10.2
GND: C1.2, C2.2, C3.2, C4.2, H1.1, H2.1, H4.1, H5.1, J1.2, J2.2, J3.2, J4.2, J5.1, J6.2, J7.2, J8.2, J9.2, J10.1, J11.2, J12.2, J14.2, J15.2, J17.1, J18.1, J20.1, J21.2, J23.2, J24.2, J25.2, J26.2, J27.2, J29.2, J30.2, J31.2, JS4.2, JS5.2, JS6.2, JS7.2, M1.2 (MS1), M1.3 (MS2), M1.9 (GND), M1.15 (GND), M2.3 (MS2), M2.9 (GND), M2.15 (GND), M3.2 (MS1), M3.9 (GND), M3.15 (GND), M4.9 (GND), M4.15 (GND)

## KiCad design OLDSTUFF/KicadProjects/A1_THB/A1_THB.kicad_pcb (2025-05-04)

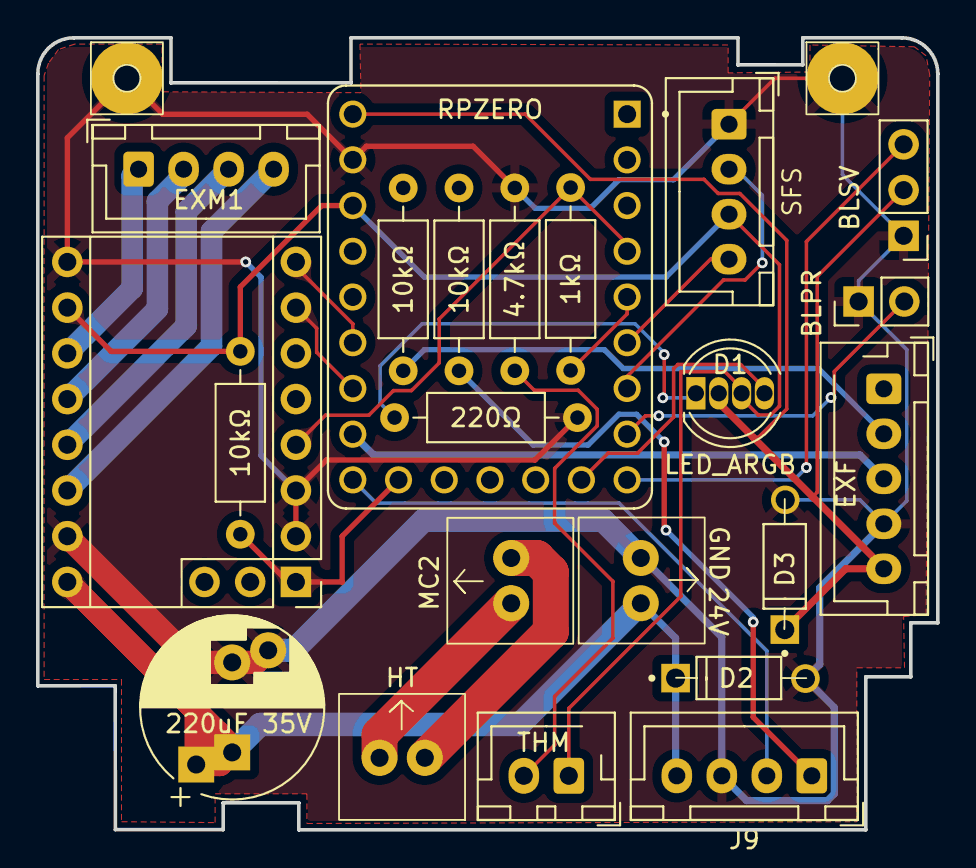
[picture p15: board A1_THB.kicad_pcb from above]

Board: 2 copper layers, 50.0 x 44.0 mm, 24 parts (0 on the bottom side), 26 nets.

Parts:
C2: 220uF 35V; CP_Radial_D10.0mm_P5.00mm_P7.50mm
D1: LED_ARGB; LED_D5.0mm-4_RGB
D2: D_PCF; Diode
D3: D_EXF; Diode
EXM1: Conn_01x04; JST_XH_B4B-XH-A_1x04_P2.50mm_Vertical
H1, H2: M1.5; Mountinghole_m1.5
J1: THM; JST_XH_B2B-XH-AM_1x02_P2.50mm_Vertical
J2: SFS; JST_XH_B4B-XH-A_1x04_P2.50mm_Vertical
J3: BLSV; PinHeader_1x03_P2.54mm_Vertical
J4: BLPR; PinHeader_1x02_P2.54mm_Vertical
J5: HT; ScrewTerminal 7mm x 7mm
J6: MC1; ScrewTerminal 7mm x 7mm
J7: MC2; ScrewTerminal 7mm x 7mm
J8: EXF; JST_XH_B5B-XH-AM_1x05_P2.50mm_Vertical
J9: PCF; JST_XH_B4B-XH-A_1x04_P2.50mm_Vertical
M1: StepperMotor; TMC2209 Footprint
R1: 1kΩ; R_Axial_DIN0207_L6.3mm_D2.5mm_P10.16mm_Horizontal
R2: 4.7kΩ; R_Axial_DIN0207_L6.3mm_D2.5mm_P10.16mm_Horizontal
R3: 220Ω; R_Axial_DIN0207_L6.3mm_D2.5mm_P10.16mm_Horizontal
R4, R5, R6: 10kΩ; R_Axial_DIN0207_L6.3mm_D2.5mm_P10.16mm_Horizontal
RPZERO1: RPZERO; RP2040-ZERO

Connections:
+3V3: D1.3 (GK), J1.1, J2.3, M1.10 (VDD), R6.2, RPZERO1.21 (3V3)
+5V: D1.2 (RK), D3.1 (K), J3.2, J8.5, RPZERO1.23 (5V)
+24V: C2.1, D2.1 (K), J6.1, J9.4, M1.16 (VM)
/BL_PR: J4.2, RPZERO1.8 (GP7)
/BL_SV: J3.3, RPZERO1.9 (GP8)
/EXF_SG: J8.3, RPZERO1.16 (GP15)
/ExtruderDriver/A1: EXM1.3, M1.13 (A1)
/ExtruderDriver/A2: EXM1.4, M1.14 (A2)
/ExtruderDriver/B1: EXM1.2, M1.12 (B1)
/ExtruderDriver/B2: EXM1.1, M1.11 (B2)
/LED_TEST: D1.4 (BK), RPZERO1.10 (GP9)
/M_DIR: M1.8 (DIR), RPZERO1.18 (GP27)
/M_EN: M1.1 (ENABLE), R6.1, RPZERO1.14 (GP13)
/M_STEP: M1.7 (STEP), RPZERO1.17 (GP26)
/M_UART: M1.4 (PDN1), R1.1, RPZERO1.4 (GP3)
/PCF_SG: J9.2, RPZERO1.15 (GP14)
/SFS_ENC: J2.2, RPZERO1.7 (GP6)
/SFS_SW: J2.4, RPZERO1.6 (GP5)
/TH_SG: J1.2, R2.1
GND: C2.2, D2.2 (A), D3.2 (A), H1.1, H2.1, J2.1, J3.1, J4.1, J6.2, J8.4, J9.3, M1.2 (MS1), M1.3 (MS2), M1.9 (GND), M1.15 (GND), R2.2, R3.2, RPZERO1.22 (GND)
unnamed: D1.1 (A), R3.1
unnamed: J5.1, J7.1
unnamed: J5.2, J7.2
unnamed: J8.2, R5.1
unnamed: J9.1, R4.1
unnamed: R1.2, RPZERO1.5 (GP4)

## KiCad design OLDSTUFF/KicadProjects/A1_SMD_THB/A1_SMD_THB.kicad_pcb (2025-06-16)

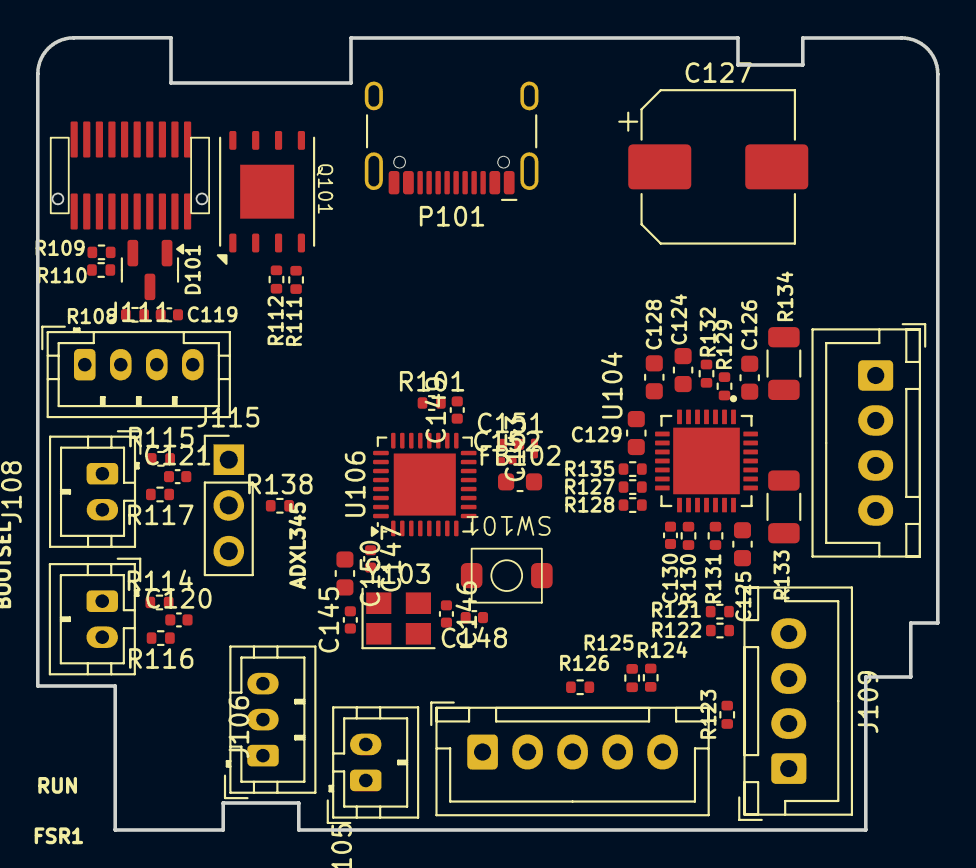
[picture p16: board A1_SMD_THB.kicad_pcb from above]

Board: 2 copper layers, 50.0 x 44.0 mm, 63 parts (0 on the bottom side), 61 nets, no tracks yet.

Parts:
C119, C120, C121, C130, C147, C148, C149: 100nF; C_0402_1005Metric
C124: 22nF 50V; C_0603_1608Metric
C125, C126, C128: 100nF 50V; C_0603_1608Metric
C127: 100uF; CP_Elec_8x10
C129: 4.7uF; C_0603_1608Metric
C145, C146: 30pF; C_0402_1005Metric
C150: 10uF; C_0603_1608Metric
C151: 10nF; C_0402_1005Metric
C152, C153: 1uF; C_0201_0603Metric
D101: BAV99; SOT-23
EXM101: Conn_01x04; JST_XH_B4B-XH-A_1x04_P2.50mm_Vertical
FB102: 120r 100MHz; C_0603_1608Metric
J104: SGDBM-08-020P-H40; Mezzanine Connector
J105: BL_PROBE; JST_PH_B2B-PH-K_1x02_P2.00mm_Vertical
J106: BL_SERVO; JST_PH_B3B-PH-K_1x03_P2.00mm_Vertical
J107: F_SR2; JST_PH_B2B-PH-K_1x02_P2.00mm_Vertical
J108: F_SR1; JST_PH_B2B-PH-K_1x02_P2.00mm_Vertical
J109: PCF_FAN; JST_XH_B4B-XH-A_1x04_P2.50mm_Vertical
J110: EXF; JST_XH_B5B-XH-A_1x05_P2.50mm_Vertical
J111: ADXL345; JST_PH_B4B-PH-K_1x04_P2.00mm_Vertical
J115: BOOT; PinHeader_1x03_P2.54mm_Vertical
P101: USB_C_Plug; USB_C_Receptacle_HCTL_HC-TYPE-C-16P-01A
Q101: NMOS; PPAK-8L 5x6 Mosfet
R101: 1k; R_0402_1005Metric
R108, R109: 2.37kR; R_0402_1005Metric
R110: 4.7kR; R_0402_1005Metric
R111: 10R; R_0402_1005Metric
R112: 20kR; R_0402_1005Metric
R114, R115: 100; R_0402_1005Metric
R116, R117: 20k; R_0402_1005Metric
R121, R122, R124, R125: 10k; R_0402_1005Metric
R123, R126: 4.7k; R_0402_1005Metric
R127, R128, R129: 20kΩ; R_0402_1005Metric
R130, R131, R132, R135: 100o; R_0402_1005Metric
R133, R134: 100mΩ; R_1206_3216Metric
R138: 10kR; R_0402_1005Metric
SW101: SW_SPST; A Stupid Button
U104: TMC2209-LA; TMC2209-LA-FOOTPRINT
U106: STM32G431KBU3; QFN-32-1EP_5x5mm_P0.5mm_EP3.45x3.45mm
Y103: Crystal_GND24; Crystal_SMD_3225-4Pin_3.2x2.5mm

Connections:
3V3: C130.2, U104.15 (VCC_IO)
+3.3VADC: D101.2 (A), R110.1
+3V3: C147.1, C149.1, C150.1, C153.1, FB102.2, J106.2, J111.1, J115.1, R129.1, U106.1 (VDD), U106.17 (VDD)
+3V3A: C151.1, C152.1, FB102.1, U106.15 (VDDA)
+5V: C129.2, U104.8 (5VOUT)
+24V: C125.2, C126.2, C127.1, C128.1, J104.1, J104.2, J104.3, J104.18, J104.19, J104.20, J109.1, J110.2, P101.A4 (VBUS), P101.A9 (VBUS), P101.B4 (VBUS), P101.B9 (VBUS), R122.1, R125.1, U104.22 (VS), U104.28 (VS)
/accelerometer/SCL: J111.4, U106.25 (PA15)
/accelerometer/SDA: J111.3, U106.30 (PB7)
/mainio/BL_PROBE: J105.2, U106.6 (PA1)
/mainio/BL_SERVO: J106.3, U106.5 (PA0)
/mainio/EXF_PWM: J110.4, R126.1, U106.29 (PB6)
/mainio/EXF_TACH: R124.1, U106.8 (PA3)
/mainio/FIL_SNS1: R115.1, U106.9 (PA4)
/mainio/FIL_SNS2: R114.1, U106.18 (PA8)
/mainio/HE_SIG: R111.1, R112.1, U106.27 (PB4)
/mainio/PCF_PWM: J109.3, R123.1, U106.28 (PB5)
/mainio/PCF_TACH: R121.1, U106.7 (PA2)
/mainio/THO: C119.1, R108.2, U106.26 (PB3)
/mcu_stm32_smol/MT_DIAG: R135.2, U106.10 (PA5)
/mcu_stm32_smol/MT_DIR: R131.1, U106.12 (PA7)
/mcu_stm32_smol/MT_EN: R132.1, U106.11 (PA6)
/mcu_stm32_smol/MT_STEP: R130.1, U106.13 (PB0)
/mcu_stm32_smol/MT_UART_RX: R101.1, U106.20 (PA10)
/mcu_stm32_smol/MT_UART_TX: R101.2, R128.2, U104.14 (~PD_UART), U106.19 (PA9)
/mcu_stm32_smol/USB_D+: P101.A6 (D+), U106.22 (PA12)
/mcu_stm32_smol/USB_D-: P101.A7 (D-), U106.21 (PA11)
GND: C119.2, C125.1, C126.1, C127.2, C129.1, C130.1, C145.2, C146.2, C148.2, C151.2, C152.2, C153.2, D101.1 (K), J104.6, J104.7, J104.14, J104.15, J107.1, J108.1, J109.2, J110.3, J111.2, J115.3, P101.A1 (GND), P101.A12 (GND), P101.B1 (GND), P101.B12 (GND), P101.S1 (SHIELD), Q101.3 (S), R112.2, R123.2, R126.2, R127.1, R128.1, R133.2, R134.2, SW101.1 (A), U104.3 (GND), U104.9 (MS1_AD0), U104.10 (MS2_AD1), U104.18 (GND), U104.29 (EXP), Y103.2, Y103.4
GND3: C120.2, C121.2, J105.1, J106.1
unnamed: C120.1, R114.2, R116.1
unnamed: C121.1, R115.2, R117.1
unnamed: C147.2, C149.2, C150.2
unnamed: D101.3 (K), R108.1, R109.2
unnamed: EXM101.1, U104.1 (OB2)
unnamed: EXM101.2, U104.26 (OB1)
unnamed: EXM101.3, U104.24 (OA1)
unnamed: EXM101.4, U104.21 (OA2)
unnamed: J104.8, J104.9, J104.10, J104.11, J104.12, J104.13, Q101.1 (D)
unnamed: J104.4, J104.5, J104.16, J104.17, R109.1, R110.2
unnamed: J107.2, R116.2
unnamed: J108.2, R117.2
unnamed: J109.4, R121.2, R122.2
unnamed: J110.5, R124.2, R125.2
unnamed: J115.2, R138.1
unnamed: P101.A5 (CC), P101.B5 (VCONN)
unnamed: Q101.2 (G), R111.2
unnamed: C148.1, SW101.2 (B), U106.4 (PG10)
unnamed: R133.1, U104.23 (BRA)
unnamed: R134.1, U104.27 (BRB)
unnamed: R127.2, U104.13 (CLK)
unnamed: C124.1, U104.5 (CPI)
unnamed: C124.2, U104.4 (CPO)
unnamed: R135.1, U104.11 (DIAG)
unnamed: R131.2, U104.19 (DIR)
unnamed: R130.2, U104.16 (STEP)
unnamed: C128.2, U104.6 (VCP)
unnamed: R129.2, R132.2, U104.2 (~EN)
unnamed: R138.2, U106.31 (PB8)
unnamed: C145.1, U106.2 (PF0), Y103.1
unnamed: C146.1, U106.3 (PF1), Y103.3
unnamed: U106.16 (VSS), U106.32 (VSS), U106.33 (VSS)
VBUS: P101.A8 (SBU1), P101.B8 (SBU2)

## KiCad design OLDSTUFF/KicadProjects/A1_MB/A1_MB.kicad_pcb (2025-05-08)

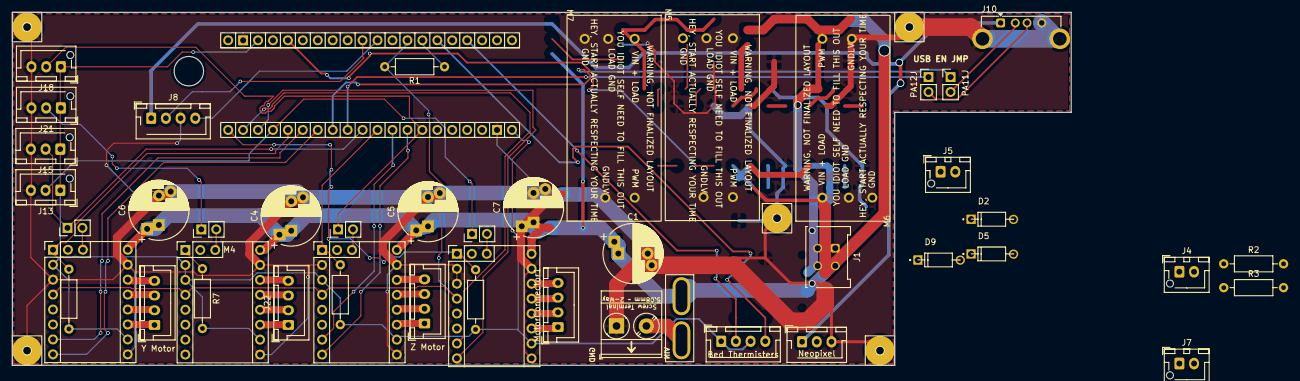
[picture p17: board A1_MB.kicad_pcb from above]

Board: 2 copper layers, 180.0 x 60.0 mm, 52 parts (0 on the bottom side), 51 nets.

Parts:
C1, C4, C5, C6, C7: 220uF; CP_Radial_D10.0mm_P5.00mm_P7.50mm
D2, D5, D9: D; Diode
F1: Mini ATO Fuse; Updated ATO Mini-Blade_2Post
H1, H2, H3, H4, H5: M1.5; Mountinghole_m1.5
J1: Molex 2x02 Microfit; Molex_Micro-Fit_3.0_43045-0412_2x02_P3.00mm_Vertical
J3: Neopixel; JST_XH_B3B-XH-AM_1x03_P2.50mm_Vertical
J4: HeatedBedConn; JST_XH_B2B-XH-AM_1x02_P2.50mm_Vertical
J5: HotendConn; JST_XH_B2B-XH-AM_1x02_P2.50mm_Vertical
J7: FanConn; JST_XH_B2B-XH-AM_1x02_P2.50mm_Vertical
J8: SmFilSns; JST_XH_B4B-XH-AM_1x04_P2.50mm_Vertical
J9: Screw_Terminal_01x02; 1x2 Terminal Block
J10: USB_A; USB_A_Connfly_DS1095
J11: Bed Thermisters; JST_XH_B4B-XH-A_1x04_P2.50mm_Vertical
J12, J14#2, J17, J20: SensorlessHoming; PinHeader_1x02_P2.54mm_Vertical
J13, J15#2, J18, J21: Endstop; JST_XH_B3B-XH-AM_1x03_P2.50mm_Vertical
J14: PA11J; PinHeader_1x02_P2.54mm_Vertical
J15: PA12J; PinHeader_1x02_P2.54mm_Vertical
J16, J19, J22: Conn_01x04; JST_XH_B4B-XH-A_1x04_P2.50mm_Vertical
M1, M2, M3, M4: TMC2209 Breakout; TMC2209 Footprint
M5, M6, M7: MosfetModule
MotorConnector1: Conn_01x04; JST_XH_B4B-XH-A_1x04_P2.50mm_Vertical
R1: 1kΩ; R_Axial_DIN0207_L6.3mm_D2.5mm_P10.16mm_Horizontal
R2, R3: 4.7kΩ; R_Axial_DIN0207_L6.3mm_D2.5mm_P10.16mm_Horizontal
R4, R5, R6, R7: 10kΩ; R_Axial_DIN0207_L6.3mm_D2.5mm_P10.16mm_Horizontal
U1: STM32 Blackpill Socketed

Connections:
+3V3: J13.1, J15#2.1, J18.1, J21.1, M1.10 (VDD), M2.2 (MS1), M2.10 (VDD), M3.3 (MS2), M3.10 (VDD), M4.2 (MS1), M4.3 (MS2), M4.10 (VDD), R2.1, R3.1, R4.2, R5.2, R6.2, R7.2, U1.18 (3V3), U1.40 (3V3)
+5V: J3.1, J8.1, J10.1 (VBUS)
+24V: C1.1, C4.1, C5.1, C6.1, C7.1, D2.1 (K), D5.1 (K), D9.1 (K), F1.1, J1.1, J1.4, J4.1, J5.1, J7.1, M1.16 (VM), M2.16 (VM), M3.16 (VM), M4.16 (VM)
/BED_THM_1: J11.2, R2.2, U1.6 (PA0)
/BED_THM_2: J11.4, R3.2, U1.4 (PC15)
/EMotor/A1: J22.3, M4.13 (A1)
/EMotor/A2: J22.4, M4.14 (A2)
/EMotor/B1: J22.2, M4.12 (B1)
/EMotor/B2: J22.1, M4.11 (B2)
/ME_DIAG: J20.1, J21.2
/ME_EN: M4.1 (ENABLE), R7.1
/MX_DIAG: J12.1, J13.2, U1.24 (PB15)
/MX_DIR: M1.8 (DIR), U1.23 (PB14)
/MX_EN: M1.1 (ENABLE), R4.1, U1.21 (PB12)
/MX_STEP: M1.7 (STEP), U1.22 (PB13)
/MY_DIAG: J14#2.1, J15#2.2, U1.30 (PA15)
/MY_DIR: M2.8 (DIR), U1.27 (PA10)
/MY_EN: M2.1 (ENABLE), R5.1, U1.25 (PA8)
/MY_STEP: M2.7 (STEP), U1.26 (PA9)
/MZ_DIAG: J17.1, J18.2, U1.34 (PB6)
/MZ_DIR: M3.8 (DIR), U1.33 (PB5)
/MZ_EN: M3.1 (ENABLE), R6.1, U1.31 (PB3)
/MZ_STEP: M3.7 (STEP), U1.32 (PB4)
/M_UART: M1.4 (PDN1), M2.4 (PDN1), M3.4 (PDN1), M4.4 (PDN1), R1.2, U1.8 (PA2)
/Mosfet1/Output_Return: D5.2 (A), J4.2
/Mosfet2/Output_Return: D2.2 (A), J1.3, J5.2
/Mosfet3/Output_Return: D9.2 (A), J7.2
/OpticSensor: J8.4, U1.10 (PA4)
/PA11: J14.1, U1.28 (PA11)
/PA12: J15.1, U1.29 (PA12)
/SwitchSensor: J8.2, U1.11 (PA5)
/UART_RX: R1.1, U1.7 (PA1)
/XMotor/A1: M1.13 (A1), MotorConnector1.3
/XMotor/A2: M1.14 (A2), MotorConnector1.4
/XMotor/B1: M1.12 (B1), MotorConnector1.2
/XMotor/B2: M1.11 (B2), MotorConnector1.1
/YMotor/A1: J16.3, M2.13 (A1)
/YMotor/A2: J16.4, M2.14 (A2)
/YMotor/B1: J16.2, M2.12 (B1)
/YMotor/B2: J16.1, M2.11 (B2)
/ZMotor/A1: J19.3, M3.13 (A1)
/ZMotor/A2: J19.4, M3.14 (A2)
/ZMotor/B1: J19.2, M3.12 (B1)
/ZMotor/B2: J19.1, M3.11 (B2)
GND: C1.2, C4.2, C5.2, C6.2, C7.2, H1.1, H2.1, H3.1, H4.1, H5.1, J1.2, J3.3, J8.3, J9.1, J10.4 (GND), J10.5 (Shield), J13.3, J15#2.3, J18.3, J21.3, M1.9 (GND), M1.15 (GND), M2.9 (GND), M2.15 (GND), M3.9 (GND), M3.15 (GND), M4.9 (GND), M4.15 (GND), U1.19 (GND), U1.39 (GND)
GNDA: J11.1, J11.3, M1.2 (MS1), M1.3 (MS2), M2.3 (MS2), M3.2 (MS1)
unnamed: F1.2, J9.2
unnamed: J12.2, M1.18 (DIAG)
unnamed: J14#2.2, M2.18 (DIAG)
unnamed: J17.2, M3.18 (DIAG)
unnamed: J20.2, M4.18 (DIAG)

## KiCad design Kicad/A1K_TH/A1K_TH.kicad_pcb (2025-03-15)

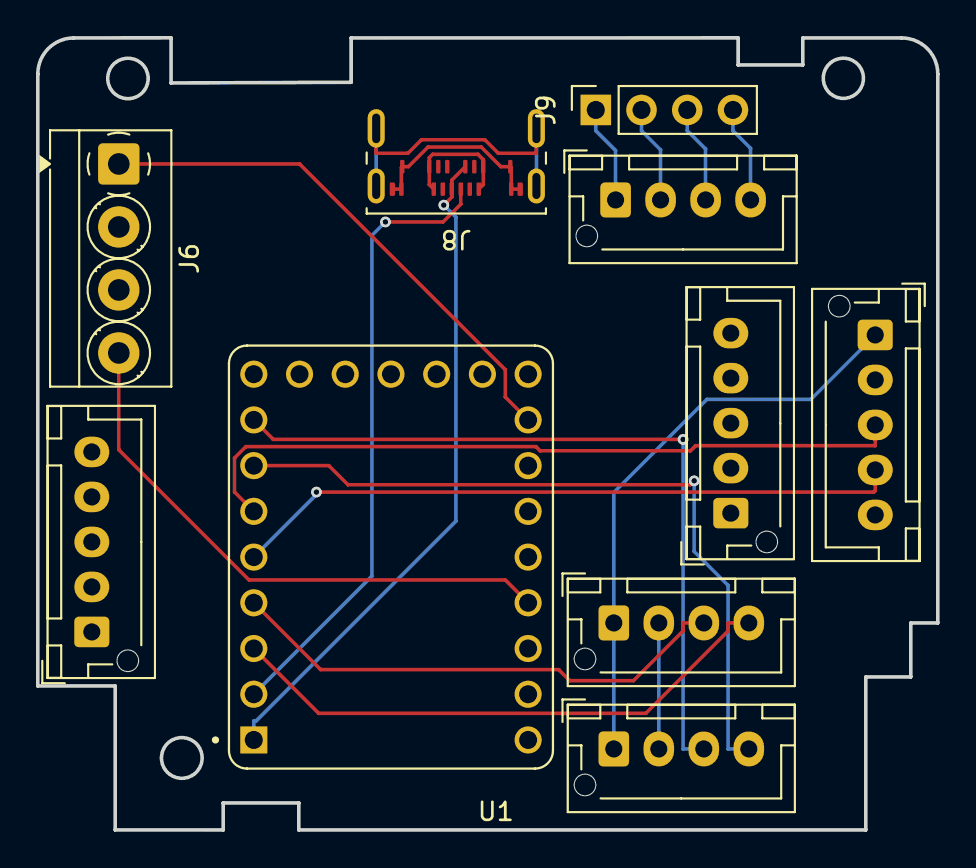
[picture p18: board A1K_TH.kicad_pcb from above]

Board: 2 copper layers, 50.0 x 44.0 mm, 10 parts (0 on the bottom side), 18 nets.

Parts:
J1: Extruder Motor; JST_XH_B4B-XH-AM_1x04_P2.50mm_Vertical
J2: Part Cooling Fan; JST_XH_B4B-XH-AM_1x04_P2.50mm_Vertical
J3: Extruder Fan; JST_XH_B5B-XH-AM_1x05_P2.50mm_Vertical
J4: Spare Fan; JST_XH_B4B-XH-AM_1x04_P2.50mm_Vertical
J5: Bed Leveling Probe; JST_XH_B5B-XH-AM_1x05_P2.50mm_Vertical
J6: Hotend and Thermister; TerminalBlock_MetzConnect_Type059_RT06304HBWC_1x04_P3.50mm_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
J7: Smart Filament Sensor; JST_XH_B5B-XH-AM_1x05_P2.50mm_Vertical
J8: USB_C_Receptacle; USB_C_Receptacle_Amphenol_124019772112A
J9: E_Motor; PinSocket_1x04_P2.54mm_Vertical
U1: RP2040-ZERO; MODULE_RP2040-ZERO

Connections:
/TH_IO/24V: J2.2, J4.2
/TH_IO/EXF_PWM: J3.4, U1.5 (GP4)
/TH_IO/EXF_TACH: J3.3, U1.6 (GP5)
/TH_IO/EXM_A1: J1.1, J9.1
/TH_IO/EXM_A2: J1.2, J9.2
/TH_IO/EXM_B1: J1.3, J9.3
/TH_IO/EXM_B2: J1.4, J9.4
/TH_IO/GND: J2.1, J3.1, J4.1
/TH_IO/HT_CT: J6.1, U1.16 (GP15)
/TH_IO/PCF_PWM: J2.4, U1.7 (GP6)
/TH_IO/PCF_TACH: J2.3, U1.8 (GP7)
/TH_IO/SPF_PWM: J4.4, U1.3 (GP2)
/TH_IO/SPF_TACH: J4.3, U1.4 (GP3)
/TH_IO/THM_SG: J6.4, U1.20 (GP29)
unnamed: J8.A1 (GND), J8.A12 (GND), J8.B1 (GND), J8.B12 (GND)
unnamed: J8.A4 (VBUS), J8.A9 (VBUS), J8.B4 (VBUS), J8.B9 (VBUS)
unnamed: J8.A7 (D-), J8.B7 (D-), U1.1 (GP0)
unnamed: J8.A6 (D+), J8.B6 (D+), U1.2 (GP1)

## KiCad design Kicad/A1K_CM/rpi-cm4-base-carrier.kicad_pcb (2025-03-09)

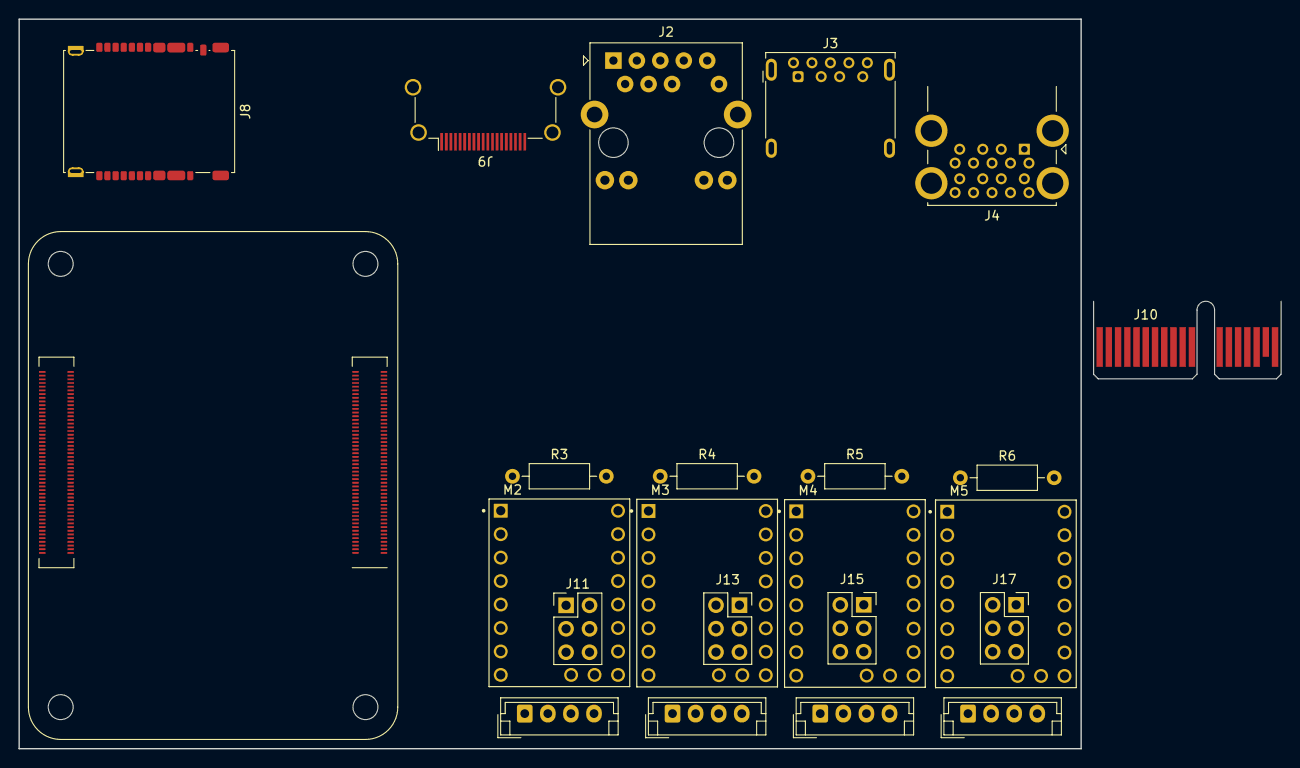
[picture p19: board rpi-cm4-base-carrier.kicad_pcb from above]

Board: 2 copper layers, 115.0 x 79.0 mm, 23 parts (0 on the bottom side), 25 nets, no tracks yet.

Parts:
J1: X_MOTOR_JST; JST_EH_B4B-EH-A_1x04_P2.50mm_Vertical
J2: RJ45; RJ45_Abracon_ARJP11A-MA_Horizontal
J3: USB3_A; USB3_A_Molex_48393-001
J4: USB_A_Stacked; USB3_A_Molex_48406-0001_Horizontal_Stacked
J5: Y_MOTOR_JST; JST_EH_B4B-EH-A_1x04_P2.50mm_Vertical
J6: Z_MOTOR_JST; JST_EH_B4B-EH-A_1x04_P2.50mm_Vertical
J7: S_MOTOR_JST; JST_EH_B4B-EH-A_1x04_P2.50mm_Vertical
J8: Micro_SD_Card; SD-SIM_microSD-microSIM_Molex_104168-1620
J9: HDMI_A_1.4; HDMI_A_Amphenol_10029449-x01xLF_Horizontal
J10: Bus_PCI_Express_x1; BUS_PCIexpress_x1
J11: Conn_02x03_Odd_Even; PinHeader_2x03_P2.54mm_Vertical
J13, J15, J17: Conn_02x03_Odd_Even; PinSocket_2x03_P2.54mm_Vertical
M2, M3, M4, M5: TMC2209 Breakout; MODULE_TMC2209_SILENTSTEPSTICK
Module1: ComputeModule4-CM4; Raspberry-Pi-4-Compute-Module
R3, R4, R5, R6: 10kΩ; R_Axial_DIN0207_L6.3mm_D2.5mm_P10.16mm_Horizontal

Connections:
+1.8V: Module1.88 (+1.8v_(Output)), Module1.90 (+1.8v_(Output))
+3.3V: Module1.78 (GPIO_VREF(1.8v/3.3v_Input)), Module1.84 (+3.3v_(Output)), Module1.86 (+3.3v_(Output))
+3V3: M2.10 (VDD), M3.10 (VDD), M4.10 (VDD), M5.10 (VDD), R3.2, R4.2, R5.2, R6.2
+5V: Module1.77 (+5v_(Input)), Module1.79 (+5v_(Input)), Module1.81 (+5v_(Input)), Module1.83 (+5v_(Input)), Module1.85 (+5v_(Input)), Module1.87 (+5v_(Input))
/TMC Modules/CLK: J11.3, J13.3, J15.3, J17.3, M2.6 (CLK)
/TMC Modules/COIL-A1: M2.13 (A1), M3.13 (A1), M4.13 (A1), M5.13 (A1)
/TMC Modules/COIL-A2: M2.14 (A2), M3.14 (A2), M4.14 (A2), M5.14 (A2)
/TMC Modules/COIL-B1: M2.12 (B1), M3.12 (B1), M4.12 (B1), M5.12 (B1)
/TMC Modules/COIL-B2: M2.11 (B2), M3.11 (B2), M4.11 (B2), M5.11 (B2)
/TMC Modules/DIAG: J11.1, J13.1, J15.1, J17.1
/TMC Modules/PDN2: J11.6, J13.6, J15.6, J17.6, M2.5 (PDN2)
/TMC Modules/S_DIAG_INT: J17.2, J17.4, M5.18 (DIAG)
/TMC Modules/S_ENABLE: M5.1 (ENABLE), R6.1
/TMC Modules/VIN: M2.16 (VM), M3.16 (VM), M4.16 (VM), M5.16 (VM)
/TMC Modules/X_DIAG_INT: J11.2, J11.4, M2.18 (DIAG)
/TMC Modules/X_ENABLE: M2.1 (ENABLE), R3.1
/TMC Modules/Y_DIAG_INT: J13.2, J13.4, M3.18 (DIAG)
/TMC Modules/Y_ENABLE: M3.1 (ENABLE), R4.1
/TMC Modules/Z_DIAG_INT: J15.2, J15.4, M4.18 (DIAG)
/TMC Modules/Z_ENABLE: M4.1 (ENABLE), R5.1
GND: M2.9 (GND), M2.15 (GND), M3.9 (GND), M3.15 (GND), M4.9 (GND), M4.15 (GND), M5.9 (GND), M5.15 (GND), Module1.1 (GND), Module1.2 (GND), Module1.7 (GND), Module1.8 (GND), Module1.13 (GND), Module1.14 (GND), Module1.22 (GND), Module1.23 (GND), Module1.32 (GND), Module1.33 (GND), Module1.42 (GND), Module1.43 (GND), Module1.52 (GND), Module1.53 (GND), Module1.59 (GND), Module1.60 (GND), Module1.65 (GND), Module1.66 (GND), Module1.71 (GND), Module1.74 (GND), Module1.98 (GND), Module1.107 (GND), Module1.108 (GND), Module1.113 (GND), Module1.114 (GND), Module1.119 (GND), Module1.120 (GND), Module1.125 (GND), Module1.126 (GND), Module1.131 (GND), Module1.132 (GND), Module1.137 (GND), Module1.138 (GND), Module1.144 (GND), Module1.150 (GND), Module1.155 (GND), Module1.156 (GND), Module1.161 (GND), Module1.162 (GND), Module1.167 (GND), Module1.168 (GND), Module1.173 (GND), Module1.174 (GND), Module1.179 (GND), Module1.180 (GND), Module1.185 (GND), Module1.186 (GND), Module1.191 (GND), Module1.192 (GND), Module1.197 (GND), Module1.198 (GND)
unnamed: J10.A9 (+3.3V), J10.A10 (+3.3V), J10.B8 (+3.3V)
unnamed: J10.A2 (+12V), J10.A3 (+12V), J10.B1 (+12V), J10.B2 (+12V), J10.B3 (+12V)
unnamed: J10.A4 (GND), J10.A12 (GND), J10.A15 (GND), J10.A18 (GND), J10.B4 (GND), J10.B7 (GND), J10.B13 (GND), J10.B16 (GND), J10.B18 (GND)
SPI_MISO: J11.5, J13.5, J15.5, J17.5

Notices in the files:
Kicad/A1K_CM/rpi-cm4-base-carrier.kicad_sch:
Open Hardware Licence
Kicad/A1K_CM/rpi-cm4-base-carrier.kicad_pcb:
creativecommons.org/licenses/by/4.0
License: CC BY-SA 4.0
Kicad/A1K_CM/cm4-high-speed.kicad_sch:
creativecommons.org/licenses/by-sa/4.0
